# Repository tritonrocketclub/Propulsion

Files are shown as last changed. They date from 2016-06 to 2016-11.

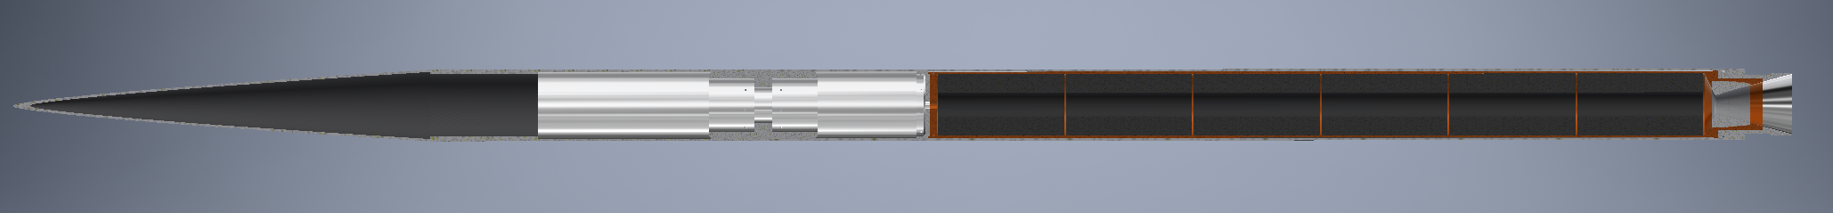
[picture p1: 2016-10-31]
Launches/8-inch-flight/Design/CAD/Vehicle/full_vehicle.PNG

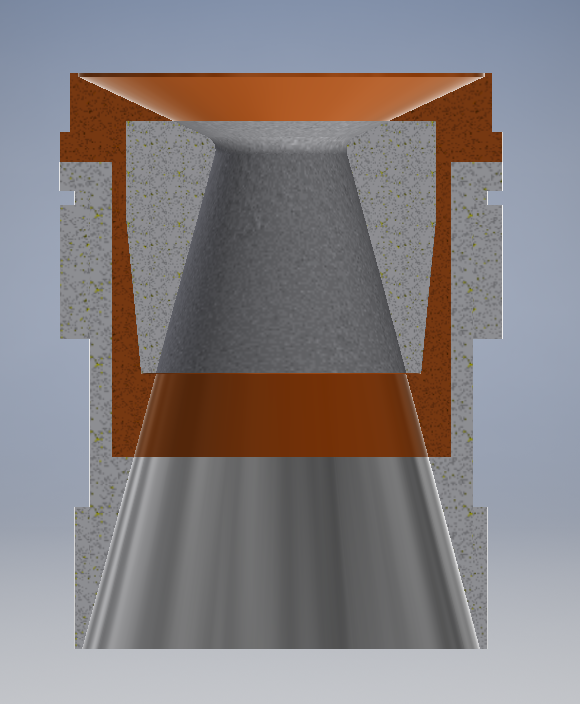
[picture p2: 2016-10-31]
Launches/8-inch-flight/Design/CAD/Vehicle/nozzle.png

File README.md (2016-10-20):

# Propulsion

Triton Rocket Club's Propulsion Team Repository.

## Overview
The Propulsion Team is resposible for designing and manufacturing the propulsion system for all TRC launches. Historically, TRC has created single stage, solid motor rockets to achieve their goals. Starting in Fall of 2016, TRC will begin research into liquid propulsion systems, however, this will remain a research only project until further notice.

## Current Projects
### Intrepid Rocket
* Q-motor
* extimated altitude of 50km
* 7.5s burn time
* Aluminum APCP

### Liquid Propellant Engine
Research phase only.
* Isopropyl Alcohol and Nitrogen Tetroxide (fuel and oxidize)
* targeting 1000lb thrust
* reneratively cooled
* pressure fed

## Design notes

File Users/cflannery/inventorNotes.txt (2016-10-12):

Autodesk Inventor Tutorial:

<User Interface>
 - creating files
 - file types
  - how files are stored
 - browser and panel bar in assembly, part, presentation, and drawing environments
 
 <Inventor My Home>
  -Getting Started
  -Team Web(configure for Triton Rocket Club)
  -Help Documentation
  
 <New>
  -parts
  -assemly
  -presentation
  -drawing
  
  -Expand new panel to select more advanced templates (Create TRC templates)
  
 <Recent Documents>
  - can be opened immediately
  - My Home Screen will remain in the bottom as a tab
 <Recent Documents/>
 
 <Environments>
  <File Extensions>
   Assembly Files .iam
   Part Files .ipt
   Drawing Files .dwg
	-industry standard file type for drawings
   Inventor Drawing Files .idw
  <File Extensions/>
  <Template Files>
   TRC has/will be making their own templates for part files and drawing files
   Ensures consistent units
  <Template Files/>
  <Part Modeling Environment>
   Create and edit 3D parts
   interface will adjust to present tools for your current task
  <Part Modeling Environment/>
  <Assembly Modeling Environment>
   Build and edit 3D assembly models 
   components are referenced in assemblies, part data still lives in part file
  <Assembly Modeling Environment/>
  <Presentation Environment>
   Create exploded assembly views
   record animations
   presentation files reference assembly files
  <Presentation Environment/>
  <Drawing Environment>
   Create 2D drawings of parts and assemblies
   References parts, assemblies, and presentation files.
  <Drawing Environment/>
 
 <Project Files>
  Dependencies between assemblies and part files will be come complicated.
  Use a projcet file to define file dependency
  
  You MUST have an active project before creating any files
   - on the bottom of the "Create New File" Dialogue
 <Project Files/>
 
 <File Types>
 
 <File Types/>

  <Parts>
   Parts are their own entity
   Stored in their own files
   Can be used in multiple Assemblies
   Changes to part files will be reflected in Assemblies
  <Parts/>
  <Assemblies>
   Can be referenced in other assembly files, presentation files, and drawing files

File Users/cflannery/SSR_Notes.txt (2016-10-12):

System Design Review Notes

Big picture, high level design for 8-inch launch

Intrepid:
* shall be a rocket
* must be scalable for the "space launch"
* altitude goal/motor class?
 - defined by motor class
 - Q motor
 - 125k feet
 
 stability margin
 
 2 stage rocket
 
Jared says we can't do large 2 stage bc of faa

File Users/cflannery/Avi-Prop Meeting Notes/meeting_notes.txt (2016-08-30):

Meeting Notes:

SLV:
- prop may have to take over SLV
- should consider making a two stage rocket
- I will look into the quantitative justification for using a two stage rocket

Second stage:
- good engineering challenge
- mechanical design
- electrical design
- actuators?
- second stage engine can extend into interstage
- interstages are sexy

- actuators are complex
 - they are a good engineering challenge
 
Flight Computer:
- triple redundancy?
- interstage controller
- meche design
 - have people design mechanical enclosuers
- RIOs
 - thermal
 - pducer
 - transmit
 - video
  
- Second stage flight computer:
 - clone of first stage

- This design can be brought to the design review with SpaceX

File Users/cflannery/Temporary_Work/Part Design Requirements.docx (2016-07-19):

I) Nozzle Retaining Ring
  A) Must have at least ½” wall thickness
  B) Forward end must have space for a ¼” or thicker o-ring on the outer diameter
    1) O-ring groove requirements
      (a) Groove height must be <80% of thickness of ring to ensure compression
      (b) Groove OD cannot allow for less than 50% of retainer to come into contact with nozzle
      (c) Groove must give adequate compression to hold o-ring on with a small amount of stretch
        (i) Reference McMaster Carr website for “actual” dimensions of o-rings
    2) Purpose is for sealing the motor’s aft end
    3) Thicker o-rings for larger motors is not a requirement, but margins become tight
  C) Must be long enough to contain pins at least 2x pin diameter from top or bottom
    1) Makes sure that there is no failure in the retainer due to yielding
    2) Drilling is not perfectly accurate, and leeway must be given for drill to work properly
II) Nozzle Basic Requirements
  A) Phenolic must be glued on top of the graphite section to ensure that there are no joints parallel to flow direction
  B) Graphite and phenolic inserts must be in compression during firing by use of steps
    1) Step thickness must be ~10% of motor diameter
  C) A 1” length of phenolic must mate with the ID of the casting tube
    1) Ensures that no heated gas flows to the aluminum
    2) Additionally allows for pressure to reach cavity between aluminum and phenolic
      (a) If a single flow path is not generated then the phenolic must take the pressure, and will crack, leading to failure
  D) Sections must be mated using a high temperature epoxy (IE JB-weld), and will have final profile machined as a single piece
  E) Nozzle internal profile does not need to be exact, but no sharp angles can be created in flow path Part Specific Nozzle Requirements
III) Specific Requirements
  A) Graphite Requirements
    1) Minimum thickness must be greater than 10% of motor diameter
    2) Minimum thickness at throat must be greater than 25% motor thickness, or 6”, whichever is smaller
      (a) Only allowance is if the throat is greater than 4”, then a 2” thickness is required
    3) Section must be long enough that 15o diverging half angle is reached 1” before bottom of nozzle
    4) Section must be long enough so that aft end is 166% ID of the throat
    5) OD must be roughed for gluing into phenolic
  B) Phenolic requirements
    1) 1.5” sections must be

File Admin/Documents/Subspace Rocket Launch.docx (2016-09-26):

# Subspace Rocket Launch

Triton Rocket Club

31 August 2016

# Preface

## Vehicle Designation

Henceforth, this launch vehicle will be referred to as No More Mr Nice Guy. Taking a page from SpaceX, this vehicle is named after a ship from Iain M. Banks’ Culture Series.

# Section 1: Project Overview

## 1.1 Introduction

The Triton Rocket Club is pursing the goal of being the first undergraduate university organization to launch a rocket past the Van Karmen line, 100 km, which is commonly known as the edge of space. In working towards achieving this goal, the club has been building incrementally larger solid motor rockets, making improvements each time based on empirical data.

This document outlines the design of the final launch before the club attempts the space shot.

## 1.2 Design Teams

This section will outline the design teams for the project

## 1.3 Design Reviews

This section will outline the standard design review process for any system on the rocket

## 1.4 Launch Readiness Review

This section will outline the process for determining launch readiness of No More Mr Nice Guy.

## 1.5 Mission Success/Failure

How to determine if the mission is a success or failure. A successful mission will permit TRC to continue with the development of the Space Shot Vehicle.

# Section 2: Design Criteria

## 2.1 Altitude

The target altitude for No More Mr Nice Guy is 50 km.

## 2.2 Two Stage Design

The TRC Two-Stage Vehicle is designed with the goal of achieving a higher altitude with a smaller mass ratio. Furthermore, building a two-stage rocket provides a unique challenge for all the engineering groups. This allows for the organization to perform one of its main functions; the development of good engineers. The discussion below covers the design criteria for each department and team with in TRC in relation to building a two stage vehicle.

## 2.3 Propulsion

Propulsion for No More Mr Nice Guy should demonstrate remote ignition capabilities of the second stage.

## 2.3.1 First Stage

Initial ascent.

## 2.3.2 Second Stage

Secondary ascent. Apogee of at least 50 km.

## 2.3.3 Thermal

Propulsion thermal team is responsible for instrumenting the vehicle and measuring thermal data against models

## 2.4 Avionics

Avionics has a lot of stuff.

- Design

## 2.4.1 Flight Computer

## 2.4.2 RIO

## 2.4.3 Instrumentation

## 2.4.4 Telemetry

## 2.4.5 Power

## 2.4.6 RF

Avionics RF is responsible for communication between the rocket and the ground station.

## 2.5 Space Launch Vehicle

The Space Launch Vehicle is the design of both the first and second stage of No More Mr Nice Guy. The design should ensure that cost, in terms of materials, weight, and size, are minimized by using a two-stage vehicle as opposed to a single stage.

Possible to reduce mass by using COPV?

## 2.6 Structures

Rephrase to conform to highlight design criteria

Structures for No More Mr Nice Guy requires a launch tower that can accommodate a two-stage vehicle. The current launch tower is capable of housing a two-stage rocket. Holes must be drilled to adjust the launch rails to the appropriate rocket diameter. The logistics of transportation of the tower currently requires two trucks due to each half of the tower being 8’ tall and having a base of 3’ x 3’. Lifting the tower with a heavy rocket inside it will require a few people and ropes, potentially with the assistance of a winch.

## 2.7 Launch Operations

Launch Operations primary function is to ensure launch conditions are sufficient for launch. Launch Operations will also receive telemetry from the rocket and monitor its performance.

## 2.8 Payload

TBD if a scientific payload will be launched on No More Mr Nice Guy.

# Section 3: Data Analysis and Processing

What data are we getting back from this launch, why, and what are we going to do with it.

- Confirmation of design for Space Shot
- Identification of any failure modes
- Engineering challenge for students

# Section 4: Launch Facility

Details about the launch facility. Black rock? Must support altitude of 50 km.

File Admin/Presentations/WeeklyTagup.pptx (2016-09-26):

## Propulsion Weekly Tagup

12 September 2016

## Agenda

- Two-Stage Calculations
- NASA Sounding Rockets

## Two-Stage Calculations

- Assume two equal stages (nonideal)

## NASA Sounding Rockets

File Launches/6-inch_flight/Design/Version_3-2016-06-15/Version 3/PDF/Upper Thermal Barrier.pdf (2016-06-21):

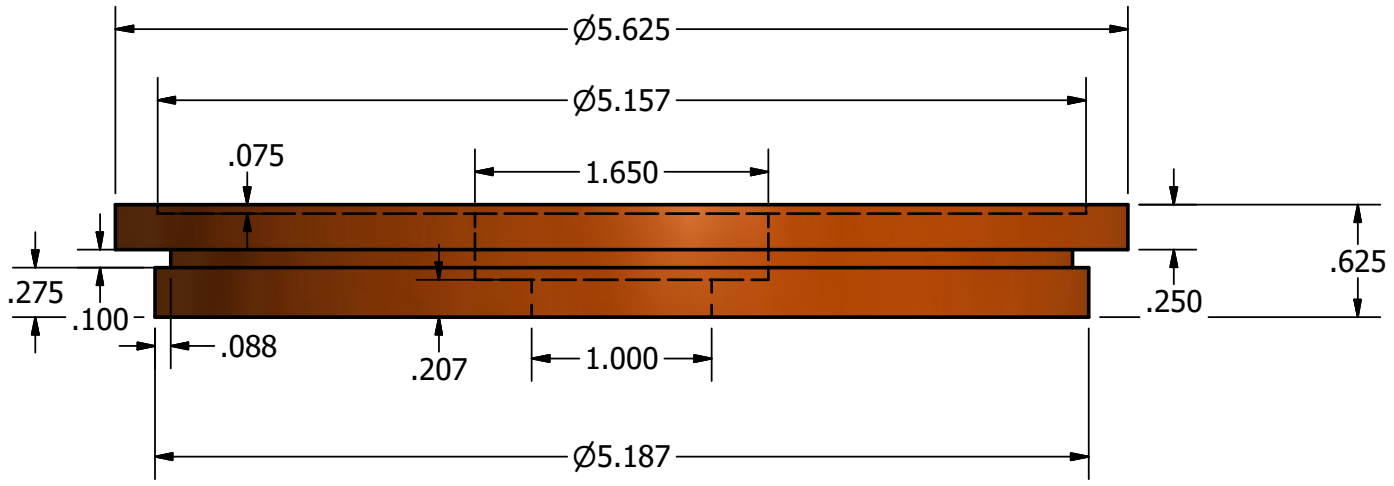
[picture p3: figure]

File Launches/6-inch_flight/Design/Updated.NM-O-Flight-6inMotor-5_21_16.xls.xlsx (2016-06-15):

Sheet: Bates Grain Kn Calculator
Bates Grain Kn Calculator | Version 2K |  |  |  |  | 541.1623662 | Max Psi
 |  |  |  |  |  | 527.5492347 | Avg Psi
 |  |  |  |  |  | 1435.83065 | Max Thrust (lbf) |  |  |  |  |  |  |  |  | Throat
Number of Grains: | 4 |  | boundry layer |  |  | 1396.14471 | Avg Thrust (lbf) |  |  |  |  |  |  |  |  | Diameter
Grain OD (OD Casting: | 5.187 |  | 0.005 |  |  | 4.50 | Burn Time (s) |  |  |  |  |  |  |  |  | Rate
Core Diameter: | 3.250 | Core Di (in) |  |  |  | 6283.861349 | Total Impulse (lbf*s) |  |  |  |  |  |  |  |  | 0
Grain Length: | 10 | 3 |  |  |  | 0 | Isp |  |  |  |  |  |  |  |  |  |  |  |  |  |  | outer
Nozzle Throat Diameter: | 1.5 | 3.2 |  |  |  |  |  |  |  |  | BurnA1 | BurnA2 | Each grain |  |  | equ nozzle | Nozzle |  | nozzle |  |  | nozzle
Final Nozzle Throat Diameter | 1.5 | 3.3 |  | Burn | OD-Initial | Length | Core dia | Outside | End area | Core End | End area | Core burn | Total burn | Area x number | Web | Throat | Throat | Kn Ratio (w/ boundary | throat |  |  | throat
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

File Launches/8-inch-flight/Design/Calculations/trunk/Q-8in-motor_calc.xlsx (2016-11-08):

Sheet: Bates Grain Kn Calculator
Bates Grain Kn Calculator |  | Version 2K |  |  |  |  | Outputs |  |  |  |  |  |  |  |  | Okay to Calculate: |  | TRUE
Mission: |  | Q-Motor
 |  |  |  |  |  |  | Burn Increment: |  | 0.1431 | [in/step] |  | Max Psi: |  | 642.2202061
Number of Grains: |  | 6 | # | Grain Core Diameters (in) |  |  | Initial burn surface: |  | 1103.1467 |  |  | AVG Psi: |  | 586.5227509 |  | Error Checking
Grain OD (ID Casting): |  | 6.9 | [in] |  |  |  | Nozzle throat area: |  | 4.011 | *no boundry |  | Max Thrust (lbf): |  | 3972.217478
Core Diameter: |  | 2.75 | [in] | 3 |  | # | Initial Kn: |  | 277.4459259 |  |  | Avg Thrust (lbf): |  | 3600.392678
Grain Length: |  | 14 | [in] | 3 |  | # | Kn Max: |  | 334.5264738 |  |  | Burn Time (s): |  | 9.236801475
Nozzle Throat Diameter: |  | 2.26 | [in] | 3 |  | # | Final Kn: |  | 322.2044444 |  |  | Total Impulse (lbf*s): |  | 32626.64886
Final Nozzle Throat Diameter: |  | 2.26 | [in] | 3.4 |  | # |  |  |  |  |  | Erosive need below 1.4: |  | 1.184060106
Nozzle Exit Dia: |  | 6 | [in] | 3.8 |  | # | "Ideal" Bates length: |  | 11.7250 | (See Note 4)
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

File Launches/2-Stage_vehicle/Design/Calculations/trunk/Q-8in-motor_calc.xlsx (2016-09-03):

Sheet: Bates Grain Kn Calculator
Bates Grain Kn Calculator |  | Version 2K |  |  |  |  | Outputs |  |  |  |  |  |  |  |  | Okay to Calculate: |  | TRUE
Mission: |  | Q-Motor
 |  |  |  |  |  |  | Burn Increment: |  | 0.1257 | [in/step] |  | Max Psi: |  | 745.9793426
Number of Grains: |  | 6 | # | Grain Core Diameters (in) |  |  | Initial burn surface: |  | 1261.6470 |  |  | AVG Psi: |  | 698.3950626 |  | Error Checking
Grain OD (ID Casting): |  | 7.062 | [in] |  |  |  | Nozzle throat area: |  | 4.011 | *no boundry |  | Max Thrust (lbf): |  | 4622.400088
Core Diameter: |  | 3.416666667 | [in] | 3 |  | # | Initial Kn: |  | 317.3093915 |  |  | Avg Thrust (lbf): |  | 4301.691088
Grain Length: |  | 14 | [in] | 3 |  | # | Kn Max: |  | 357.8910079 |  |  | Burn Time (s): |  | 7.500291867
Nozzle Throat Diameter: |  | 2.26 | [in] | 3 |  | # | Final Kn: |  | 346.6650359 |  |  | Total Impulse (lbf*s): |  | 32181.17732
Final Nozzle Throat Diameter: |  | 2.26 | [in] | 3.4 |  | # |  |  |  |  |  | Erosive need below 1.4: |  | 1.30036548
Nozzle Exit Dia: |  | 9 | [in] | 3.8 |  | # | "Ideal" Bates length: |  | 12.3013 | (See Note 4) |  | Isp[s]: |  | 217.8164393 | [s]
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

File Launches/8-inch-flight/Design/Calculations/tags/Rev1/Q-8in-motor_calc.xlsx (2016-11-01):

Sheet: Bates Grain Kn Calculator
Bates Grain Kn Calculator |  | Version 2K |  |  |  |  | Outputs |  |  |  |  |  |  |  |  | Okay to Calculate: |  | TRUE
Mission: |  | Q-Motor
 |  |  |  |  |  |  | Burn Increment: |  | 0.1431 | [in/step] |  | Max Psi: |  | 642.2202061
Number of Grains: |  | 6 | # | Grain Core Diameters (in) |  |  | Initial burn surface: |  | 1103.1467 |  |  | AVG Psi: |  | 586.5227509 |  | Error Checking
Grain OD (ID Casting): |  | 6.9 | [in] |  |  |  | Nozzle throat area: |  | 4.011 | *no boundry |  | Max Thrust (lbf): |  | 3923.160089
Core Diameter: |  | 2.75 | [in] | 3 |  | # | Initial Kn: |  | 277.4459259 |  |  | Avg Thrust (lbf): |  | 3550.87038
Grain Length: |  | 14 | [in] | 3 |  | # | Kn Max: |  | 334.5264738 |  |  | Burn Time (s): |  | 9.236801475
Nozzle Throat Diameter: |  | 2.26 | [in] | 3 |  | # | Final Kn: |  | 322.2044444 |  |  | Total Impulse (lbf*s): |  | 32626.64886
Final Nozzle Throat Diameter: |  | 2.26 | [in] | 3.4 |  | # |  |  |  |  |  | Erosive need below 1.4: |  | 1.184060106
Nozzle Exit Dia: |  | 9 | [in] | 3.8 |  | # | "Ideal" Bates length: |  | 11.7250 | (See Note 4)
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

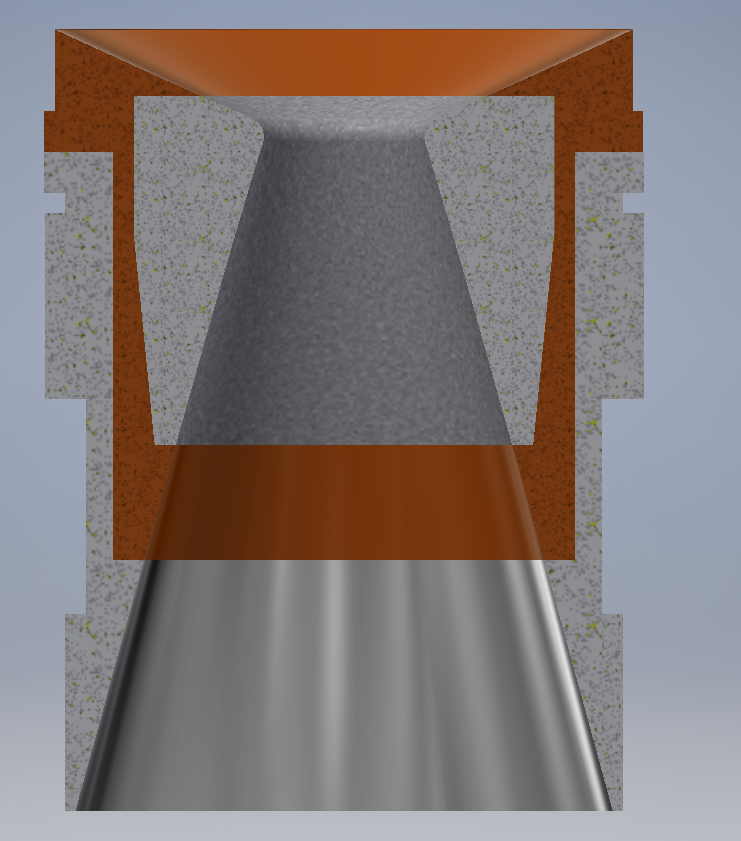
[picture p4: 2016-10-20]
Launches/8-inch-flight/Design/CAD/Vehicle/Nozzle/sectionView.PNG

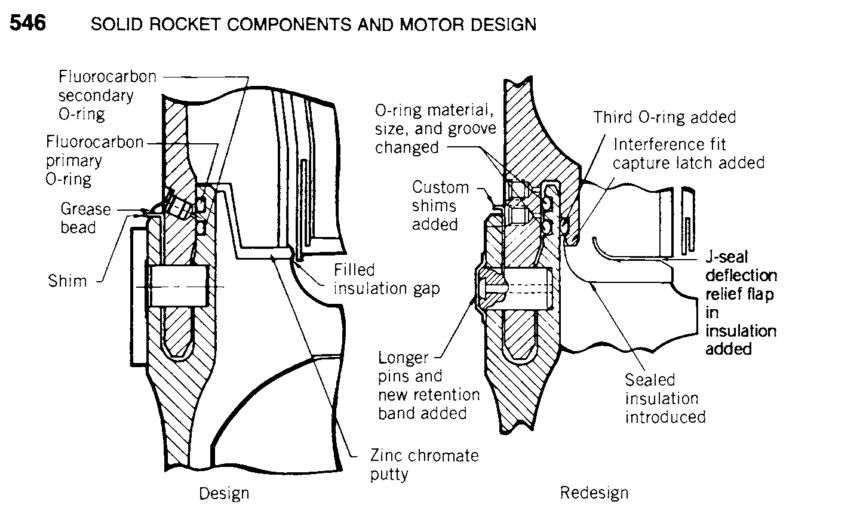
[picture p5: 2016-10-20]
Launches/8-inch-flight/Design/CAD/Vehicle/Nozzle/O-ring_SRBs.PNG

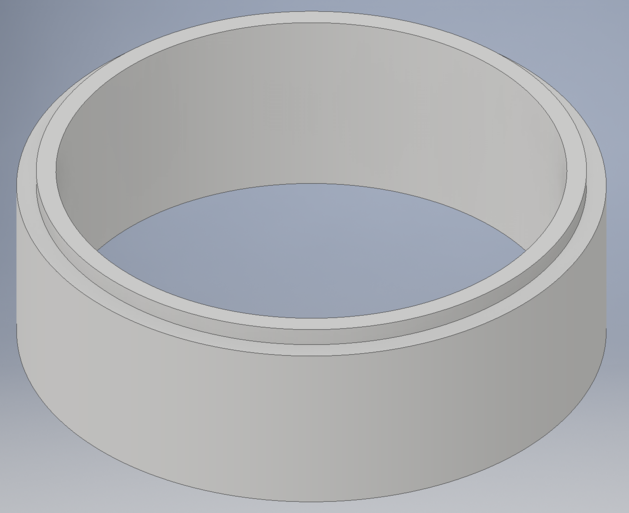
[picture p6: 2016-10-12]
Users/blieu/Images/Retainer.PNG

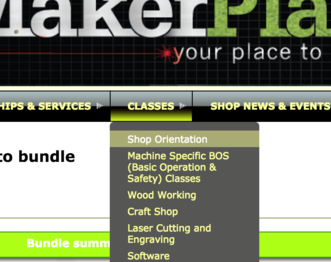
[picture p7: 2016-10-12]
Users/blieu/Images/classes.png

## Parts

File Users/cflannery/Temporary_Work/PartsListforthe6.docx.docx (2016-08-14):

# 6” Comprehensive Parts List

Reference for 8” and 10”

https://drive.google.com/folderview?id=0BxXyjHIezGQrbno0R293bmlCUVU&usp=drive_web

# Propulsions

- Graphite throat for nozzle - FE250 lathed from 4x4x6” block for 6” static fire from Kevin Anderson <KevinA@etm-lb.com>, bought G330 (higher grade, more density needed) for 6” flight, G330 will be needed for all further flights as well
- Phenolic carrier for nozzle - “Machinable Garolite (LE)” from McMaster-Carr, lathed from multiple blocks 1.5” thick epoxied onto each other, could possibly buy rod version instead for future as it will be one piece : http://www.mcmaster.com/#garolite/=121yfgj
- Aluminum carrier for nozzle - from 6061-T6 stock at IMS, lathed to design
- Forward Bulkhead, Aluminum 6061-T6 stock at IMS lathed to design
- Casting Tubes ( Paper Reinforced XX Tubing 5.375 OD x 5.187 ID x .093 Wall 9 Feet Min Order ) ordered from http://k-mac-plastics.com/xx-laminate-tubes.htm
- Phenolic Liners (5.375 ID x .125 Wall) ordered from: Scott Kormier of Loki Rocketry
- Aluminum 6061-T6 motor casing- 6” OD, 3/16”(.1875) wall thickness: drilled holes in side for pin slots
- Pull Out Dowel Pins from Mcmaster-Carr for nozzle and forward bulkhead
  - http://www.mcmaster.com/#standard-dowel-pins/=121yho0

GENERAL: Aeropoxy+Filler

White Lithium Grease

multipurpose (silicone) orange http://www.mcmaster.com/#o-rings/=121yjuk (when in doubt lower 0 rings size)

Igniters (from Jon Newman)

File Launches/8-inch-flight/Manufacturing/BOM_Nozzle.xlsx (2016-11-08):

Nozzle Part | Material | Dimensions | Supplier | Notes
Graphit Throat for Nozzle | G330 | 5.26"x5.26"x4.25" | Kevin Anderson contacted at KevinA@etm-lb.com | http://www.tokaicarbon.co.jp/en/products/fine_carbon/isotropic.html
Phenolic Carrier | Machinable Garolite | 7.5"x7.5"x6" | http://www.mcmaster.com/#garolite/=13byhm6 | Either buy a rod or multiple 1.5'' thick blocks epoxied onto each other
Aluminum Carrier | Aluminum 6061-T6 | 7.5"x7.5"x6.9" | http://www.mcmaster.com/#aluminum-alloy-6061/=13bz6eb | Or Stock at IMS
Forward Bulkhead | Aluminum 6061-T6 |  | Same as above
Motor Casing | Aluminum 6061-T6 | 8” OD, 3/16”(.1875) Thickness | Same as above | Drilled holes in side for pin slots
Aluminum Skirt | Aluminum 6061-T6 | 7.5"x7.5"x2.5" | Same as above
Aluminum Retainer | Aluminum 6061-T6 | 7.5"x7.5"x2.734" | Same as above
Motor Liner | Phenolic Liner |  | http://www.rocketmotorparts.com/Phenolic_Liners_Uncut_Lengths/cat1577810_1455513.aspx
Casting Tubes | Pheolic Laminate Tubes Paper Reinforced XX | 5.375 OD, 5.187 ID, 0.093 Thickness | http://k-mac-plastics.com/xx-laminate-tubes.htm | Stock # : KM-22621BQ
Pull Out Dowel Pins | Stainless Steel (Type 316, 18-8, or Type 416) |  | http://www.mcmaster.com/#standard-dowel-pins/=121yho0 | For Nozzle and Forward Bulkhead
Phenolic Cap | Machinable Garolite | 7.5"x7.5"x2.5"
General
Aeropoxy + Filler
White Lithium Grease
O-Ring | Multipurpose Silicone |  | http://www.mcmaster.com/#o-rings/=121yjuk | If in doubt lower ring size
Igniters

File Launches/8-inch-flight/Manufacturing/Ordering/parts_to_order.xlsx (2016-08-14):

Bill of Materials
Item | Description | Purpose | Manufacturer | Manufacturer P/N | Supplier | Qty | Unit Cost | Total Cost | Link
1 | Graphite Block | Nozzle Throat | Electro-Tech Machining | G330 | Kevin Anderson | 1 |  |  | Kevin Anderson <KevinA@etm-lb.com
2 | Machinable Garolite (LE) | Phenolic Carrier for Nozzle | - | - | McMaster-Carr | 1
3 |  |  |  |  | Industrial Metal Supply (IMS) | 1
4
5
6
7
8
9
10
11
12
13
14
15
16
17
18
19
20
21
22
23

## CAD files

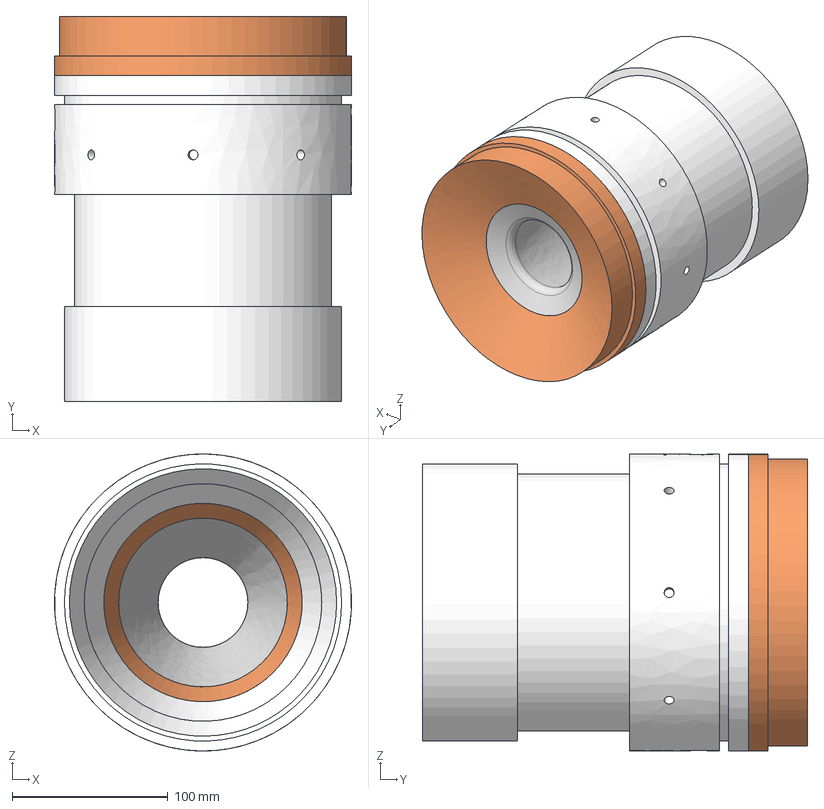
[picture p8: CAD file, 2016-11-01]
Launches/8-inch-flight/Design/CAD/Vehicle/Nozzle/trunk/nozzle.igs
190.5 x 247.2 x 190.5 mm

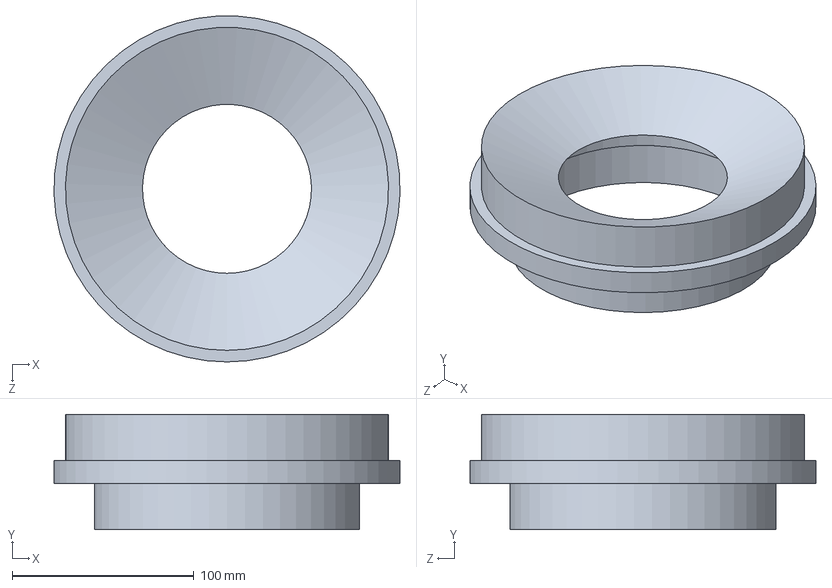
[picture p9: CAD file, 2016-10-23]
Users/cflannery/Temporary_Work/Intrepid_temp/Nozzle/SolidWorks/phenolic_liner.SLDPRT
190.4 x 63.5 x 190.3 mm

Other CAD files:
Launches/8-inch-flight/Design/CAD/Nozzle/trunk/Drawings/Aluminum Skirt.dwg
Launches/8-inch-flight/Design/CAD/Vehicle/Nozzle/trunk/Drawings/ALUMINUM_RETAINER.dwg
Users/cflannery/Temporary_Work/Intrepid_temp/Nozzle/SolidWorks/aluminum_carrier.SLDPRT
Launches/8-inch-flight/Design/CAD/Vehicle/Nozzle/trunk/Drawings/ALUMINUM_CASING.dwg
Users/cflannery/Temporary_Work/Intrepid_temp/Nozzle/SolidWorks/aluminum_retainer.SLDPRT
Launches/8-inch-flight/Design/CAD/Vehicle/Nozzle/trunk/Drawings/PHENOLIC_CARRIER.dwg
Users/cflannery/Temporary_Work/Intrepid_temp/Nozzle/SolidWorks/aluminum_boattail.SLDPRT
Launches/8-inch-flight/Design/CAD/Vehicle/Nozzle/trunk/Drawings/GRAPHITE.dwg
Users/cflannery/Temporary_Work/Intrepid_temp/Nozzle/SolidWorks/graphite.SLDPRT
Launches/8-inch-flight/Design/CAD/Vehicle/Nozzle/trunk/Drawings/PHENOLIC_CAP.dwg
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

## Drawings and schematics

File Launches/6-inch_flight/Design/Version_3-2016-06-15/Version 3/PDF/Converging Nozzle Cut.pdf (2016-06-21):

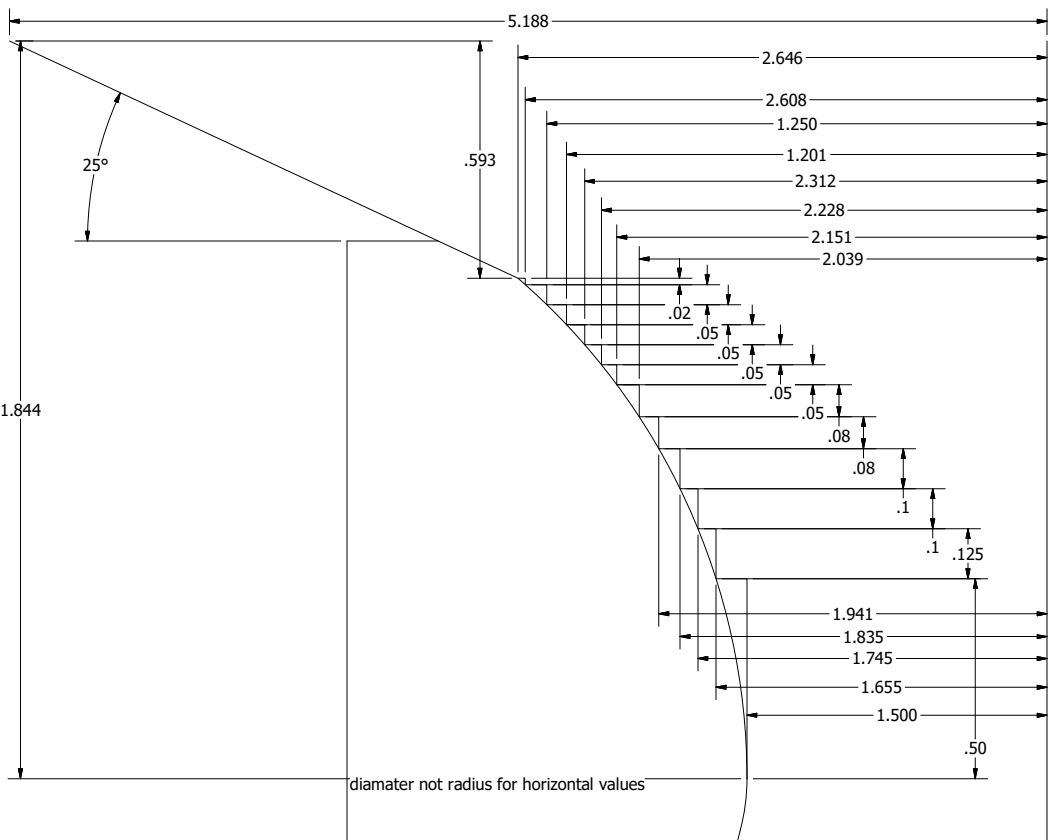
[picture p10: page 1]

diamater not radius for horizontal values

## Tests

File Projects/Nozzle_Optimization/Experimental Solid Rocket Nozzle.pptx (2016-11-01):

## Experimental Solid Rocket Nozzle

By: Cameron Flannery, Harrison Box

## Agenda

- Vehicle Overview
- Nozzle Design Overview
  - Dimensions
  - Thermal
  - Fluid Flow
- Risks

## Vehicle Overview (Major Components)

17’

7’8”


Nosecone

Recovery System

Avi-bay

BATES grains

General
- 2 piece aluminum airframe
- Aluminum section adapter
- ¾ power series nosecone
- Carbon fiber
- Note: Fins still under design review

Section Adapter

Propulsion
- Q-Class Motor
- APCP (Aluminum Fuel/Ammonium Perchlorate Oxidizer)
- Ablatively cooled nozzle
- BATES grains

Ablative Nozzle

## Nozzle Overview

Phenolic
(2-pieces)


Graphite Throat

Aluminum Retainer

Aluminum Carrier

Aluminum Skirt

## Dimensioning

Calculating Optimal Expansion Ratio*:

2.30”

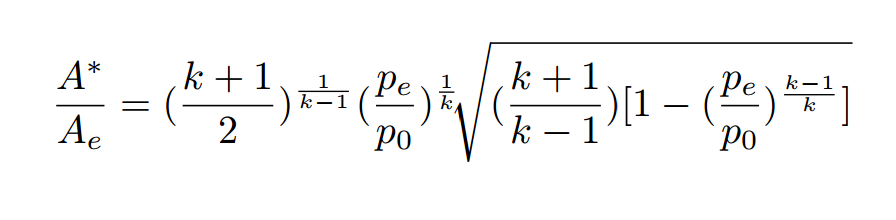
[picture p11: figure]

Ideal**: 3.1 – calculated with combustion products properties
Actual: 2.934

- Under-expansion results from manufacturing capabilities.
- Exact impact on performance is difficult to calculate due to liquid combustion products (Al)
- Performance decrease of ~5% expected

6.75”

*equation from Rocket Propulsion Elements
** at sea-level

## Nozzle Design – Stresses

Hoop Stress:

Material Properties:
- Phenolic Liner: Liner thickness; ¼”
- Heat Transfer Through Phenolic Liner: 0.15W/(m∗K)

## Nozzle Design – Fluid Flow

Aim:
- Prevent cavitation
- Prevent separation of flow
Analysis:
- CFD with ANSYS
  - Assumes gaseous combustion products
  - Results in approximately 10% error due to aluminum in propellant

## Design for Manufacturability

- 6061 Series Aluminum
- Phenolic and graphite relatively simple to machine
- Cone Nozzle:
  - Easy to machine with a lathe
  - No crazy contours
- Drawings created with GD&T for each part

## Risks

- Under-expansion is not quantified
  - Possible solution is to perform a static fires at sea-level with different expansion ratios
- Phenolic Thermal Barrier

## Q & A

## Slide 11

BACKUP SLIDES

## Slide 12

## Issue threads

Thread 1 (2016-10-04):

Nozzle Throat-Exit ratio optimization

cmflannery, 2016-10-04:
Nozzle throat-exit dimensions need to be reviewed.

cmflannery, 2016-10-04:
starting work on nozzle optimization

Bslieu99019, 2016-10-11:
**Important Links**

1. [8-inch Motor Calcs](https://github.com/tritonrocketclub/Propulsion/tree/master/Launches/8-inch-flight/Design/Calculations/trunk)
2. [Nozzle wiki](https://github.com/tritonrocketclub/Propulsion/wiki/%5BDocumentation%5D-8-inch-Rocket)

Bslieu99019, 2016-10-28:
Aluminum 6061T-6 Carrier Calculations:

Hoop stress w/ FS = 2.0 => 12.8 ksi

Thermal Stress w/ 300 F & FS = 2 => 31.7 ksi (various with temperature)
Aluminum Melting point = 1080 - 1205 °F

Tensile Strength Aluminum = 40 kpsi
Minimum thickness w/ FS = 2: 0.133125 inches

Ultimate Bursting Pressure = 3000 psi
Yield Bursting Pressure = 2666.67 psi
Maximum Pressure Experienced = 710 psi

jacquelynfirst, 2016-11-01:
I worked on the aluminum carrier with Ryan and this is what we found so far. We got a thermal stress of about 55,000psi with a temp estimate of 430 degree F change. Also Hoop stress was 7,114psi with factor of safety of 5.6.

Happy Halloween!

dtt005, 2016-11-03:
Best diameter for diverging section = 5.618in
Optimum Expansion Ratio = 6.177
Pressure experienced of aluminum skirt at exit plane = 16.546PSI (12.589% higher than atmospheric pressure)

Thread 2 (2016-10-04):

Getting more done in GitHub with ZenHub

cmflannery, 2016-10-04:
Hola! @cmflannery has created a [ZenHub](http://www.zenhub.com) account for the **tritonrocketclub** organization. ZenHub is the only project management tool integrated natively in GitHub – created specifically for fast-moving, software-driven teams.

----

#### How do I use ZenHub?

To get set up with ZenHub, all you have to do is **[download the browser extension](https://www.zenhub.com?utm_source=ZHOnboarding)** and log in with your GitHub account. Once you do, you’ll get access to ZenHub’s complete feature-set immediately.

#### What can ZenHub do?

ZenHub adds a series of enhancements directly inside the GitHub UI:

- Real-time, customizable task boards for GitHub issues;
- Multi-Repository burndown charts, estimates, and velocity tracking based on GitHub Milestones;
- Personal to-do lists and task prioritization;
- Time-saving shortcuts – like a quick repo switcher, a “Move issue” button, and much more.

### [Add ZenHub to GitHub](https://www.zenhub.com?utm_source=ZHOnboarding)

_Still curious? See [more ZenHub features](https://www.zenhub.com/features?utm_source=ZHOnboarding) or read [user reviews](https://chrome.google.com/webstore/detail/zenhub-for-github/ogcgkffhplmphkaahpmffcafajaocjbd/reviews). This issue was written by your friendly ZenHub bot, posted by request from @cmflannery._

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

Closed 2016-10-11.

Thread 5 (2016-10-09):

Avionics Integration

cmflannery, 2016-10-09:
In order to monitor motor health, the propulsion team needs chamber pressure throughout the flight. Temperature readings could also be used to confirm thermal calculations. This epic tracks the integration of the pducer into the vehicle and avionics.

The propulsion team is responsible for the mechanical design of the Avi-bay this year. The Avi-bay will be used to mount and chassis ground the flight computer.

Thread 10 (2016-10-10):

Mechanical Design for Avi Bay

cmflannery, 2016-10-10:
Design mechanical bay for avionics. Should fit snuggly and have mounting holes. Chassis ground.

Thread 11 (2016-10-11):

Quantify error due to erosive burning

cmflannery, 2016-10-11:
Determine if error due to throat ablation can be ignored in CFD analysis. Baseline Q-class motor using APCP fuel.

cmflannery, 2016-10-18:
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
- [Ablative Cooling Study](https://github.com/tritonrocketclub/Propulsion/tree/0f0267c2cab3b7e235d0b69af07ad0d52786ffc0/References/AblativeSolidRocketNozzles.pdf)

Regression due to ablative cooling can be estimated with this plot and the chamber pressure. Ablation is only estimated at the throat (graphite).

Chamber pressure ~= 4.815 MPa
Burn time ~= 7.5 s
 - from [motor calc sheet](https://github.com/tritonrocketclub/Propulsion/blob/0f0267c2cab3b7e235d0b69af07ad0d52786ffc0/Launches/8-inch-flight/Design/Calculations/tags/Rev1/Q-8in-motor_calc.xl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)

Estimated graphite regression ~= 0.17 mm/s
- based on chamber pressure & plot above

Total estimated regression ~= 0.17 mm/s * 7.5s = 1.275 mm

cmflannery, 2016-10-18:
Closing as "won't fix"  - Ablative cooling for such a short burn time does not result in significant loss of thrust due to throat area increase.

Closed 2016-10-18.

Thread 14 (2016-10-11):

Full Vehicle Mockup

cmflannery, 2016-10-11:
3D print scale model of the entire vehicle for fit checking.

cmflannery, 2016-10-21:
Rev01 nearing completion.
Todo:
* finalize airframe length
* finalize nozzle design
 * boat tail?
* finalize nose cone dimensions
* add fin can
* add faux mass for recovery system
* dimension and add avi components
* work out avi interface
 * how are we going to connect avi components 3-4' into the tube?

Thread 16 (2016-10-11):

Igniter

cmflannery, 2016-10-11:
The igniter for Intrepid presents a unique challenge. To launch a Q-class motor, we need to be ~1 mile away from the launch site. It is impractical to ignite the rocket using conventional methods; namely, we cannot run a cable from the launch site to mission control. The solution is going to be a wirelessly triggered system.

This challenge will be solved with support from Launch Ops and Avionics.

cmflannery, 2016-11-11:
Ignition will be triggered with a hot wire and a small solid rocket motor.

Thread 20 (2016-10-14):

Liner fitting into airframe

cmflannery, 2016-10-14:
The tolerances on the liner and the aluminum casing need to be large enough to allow the liner to slide into the airframe. Hoop stress calculation and material calculations should be completed on the liner to ensure the pressure in the combustion chamber doesn't cause the liner to fracture.

Look into other possible solutions.
* o-rings

Bslieu99019, 2016-10-15:
10/14 - Hoop Stress Calculations:
-FS of 1.5: ~ 31k psi
-FS of 2.0: ~ 42k psi
-Material Interest: Garolic G10: 32-40k psi (max allowable)

cmflannery, 2016-10-29:
**Phenolic Liner**
Liner thickness; 1/8"
Liner Length: 7' 10" = 94"

**Casting Tubes:**
Thickness: 1/8"
Length: 15"

**Grains**
Length: 14"
OD: 6.90"
ID: 2.75"

rlibman, 2016-11-01:
**Phenolic Liner Hoop Stress Calculations**

Using http://www.engineeringtoolbox.com/stress-thin-walled-tube-d_948.html

Hoop Stress = (745.9793426 psi * 7.062 in) / 2 * .25 in = 10536.2122348824 psi

Per http://www.g10fr4.com/g10_fr4_technical_data_specifications.html

19,000 psi max

Therefore a F.S. of ~1.8.

cmflannery, 2016-11-01:
The purpose fo the phenolic liner is to act as a thermal barrier between the combustion chamber and the aluminum casing. The phenolic liner doesn't need to take hoop stress. The heat transfer through the phenolic liner to the aluminum should be calculated and then the hoop stresses in the aluminum liner should be compared against its yield stress.

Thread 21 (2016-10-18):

Avionics Integration Design Parameters

mphalen, 2016-10-18:
The Chamber temperature and pressure ranges are needed to start planning out the avionics package. A budget estimate and desired form-factor are also welcome, but not immediately required, at this stage.

mphalen, 2016-10-26:
Chamber and pressure maximums are specified as ~710psi and ~2000C,

Closed 2016-10-26.

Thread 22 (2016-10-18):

Nozzle Dimensions and Fitting in CAD

cmflannery, 2016-10-18:
Update master sketch in Inventor and recreate assemblies and parts.

cmflannery, 2016-10-18:
[Link to rev02 directory](https://github.com/tritonrocketclub/Propulsion/tree/d85780c77f0e4c64ab95ed61d2e18549b5a94648/Launches/8-inch-flight/Design/CAD/Nozzle/tags/rev01)

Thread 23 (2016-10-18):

3D printed mock-up of nozzle

cmflannery, 2016-10-18:
Use 3D printers at library to print a mock-up of the nozzle. Scaled down to fit on printbed. Use support material where necessary.

cmflannery, 2016-10-18:
Reserve 3d printers at library [here](http://ucsd.evanced.info/dibs/Login)

Bslieu99019, 2016-10-19:
Printers Avaliable: Maker Bot: Ultimaker 2 (x1) and Replicator 2 (x2)

Instructions:
1) Two people will schedule a 3 hour block, back to back, to allow for 6 hours of printing (see above).
2) Convert Inventor file to .STL and ask model to be scaled down

Bslieu99019, 2016-10-25:
Room reserved tomorrow 10/25 3-6pm for anyone who needs to 3D print their part.

Closed 2016-10-30.

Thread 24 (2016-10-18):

GD&T Drawings of Optimized Nozzle

Bslieu99019, 2016-10-18:
It is important to create a method of communication between designer and manufacturer to minimize manufacturing errors. Read up on GD&T under references>standards for more information.

Bslieu99019, 2016-10-22:
**Components**
1. Aluminum Skirt -Danny
2. Graphite - Vickie
3. Phenolic (Both) - Hao & Jesse
4. Aluminum Carrier
5. Aluminum Retainer

**Other**
1. Aluminum Airframe

ryanjerickson, 2016-10-25:
Finished Rev.1 of Aluminum carrier

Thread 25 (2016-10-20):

Forward bulkhead seal

cmflannery, 2016-10-20:
It is important that combustion gasses don't pass the forward bulkhead. We should make sure our design prevents this. We should determine if our design is sufficient.

[SRB O-ring](https://github.com/tritonrocketclub/Propulsion/tree/master/Launches/8-inch-flight/Design/CAD/Nozzle/O-ring_SRBs.PNG)
-from RPE

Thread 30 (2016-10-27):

Section Adapter

cmflannery, 2016-10-27:
Design adapter to connect motor and recovery airframe sections

Bslieu99019, 2016-10-28:
Current Design: Inadequate For Requirements

Optimizing Requires Consideration in:
-Length
-Buckling
-Loads
-Slip
-Moment of Inertia
-Thickness

More info coming soon.

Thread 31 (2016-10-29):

Pressure Sensing

cmflannery, 2016-10-29:
Pressure measurements of the motor chamber.

cmflannery, 2016-10-29:
Need tube diameter/thread types.

mphalen, 2016-11-01:
Zirconia ceramic tube diameter set to be 1" and wall thickness is 1/4"
Thread types have yet to be decided but they can be made to order.

Length of 8" is tentative, subject to change with thermodynamic analysis.

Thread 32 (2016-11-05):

Pressure Transducer Thermodynamics

mphalen, 2016-11-05:
Need thermal transfer coefficient for motor exhaust.
Thermodynamic Analysis of Prop-Avionics Integration.

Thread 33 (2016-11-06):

RASAero Crashing when running simulations

cmflannery, 2016-11-06:
RASAero crashes when running flight simulations with our motor files.

cmflannery, 2016-11-07:
Resolved: replaced tabs between time value and thrust with single space

Closed 2016-11-07.

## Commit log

2016-06-15 General update
    added folder structure and old motor calculations
    [Updated.NM-O-Flight-6inMotor-5_21_16.xls.xlsx, Updated.NM-Q-8in-Motor-Prop-Calcs (1).xlsx, Updated.NM-S-10in-Motor-Prop-Calcs (1).xlsx]
2016-06-16 Add files via upload
    Based on designs by Jared Shapiro
    [nozzle 8in version 1.ipt]
2016-06-21 Admin info added
    see files
    [Member_Info.xlsx]
2016-06-28 Updated projectMaster
    [projectMaster.xlsx]
2016-06-28 Summer Availability
    [Member_Info.xlsx]
2016-06-28 Updated Member Info
    [Member_Info.xlsx]
2016-06-28 Retry of Updating Member Info
    [Member_Info.xlsx]
2016-07-04 new references
    [BatesCalc2K_template.xls, Updated.NM-Q-8in-Motor-Prop-Calcs (1).xlsx]
2016-07-05 Updated summer availability
    [Member_Info.xlsx]
2016-07-05 motor calculations
    working - motor calculations
    [Q-8in-motor_calc.xlsx]
2016-07-05 Motor calc updates
    [Q-8in-motor_calc.xlsx]
2016-07-06 calc updates
    [Q-8in-motor_calc.xlsx]
2016-07-06 updated projects
    [projectMaster.xlsx]
2016-07-06 project master
    [projectMaster.xlsx]
2016-07-07 Updated Motor Calc Sheet
    [Q-8in-motor_calc.xlsx]
2016-07-08 8 inch Nozzle CAD Files
    [Aluminum Carrier 8-inch v1.ipt, Aluminum Retainer 8-inch v1.ipt, Aluminum Skirt 8-inch v1.ipt]
2016-07-12 Nozzle BOM
    [Nozzle BOM.xlsx]
2016-07-13 Remaining 8 inch Nozzle CAD Files
    [Graphite 8-inch v1.0002.ipt, Graphite 8-inch v1.ipt, Nozzle 8-inch v1.0003.iam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]
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2016-07-19 Version 3 Nozzle CAD
    [Carrier.0001.ipt, Carrier.ipt, Graphite.0001.ipt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]
2016-07-20 Forward bulkhead
    [Forward Bulkhead.ipt]
2016-07-20 Edits for 7.5" fit of Retainer and Carrier
    [Carrier.0001.ipt, Carrier.0002.ipt, Carrier.ipt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]
2016-07-21 Increase OD of Nozzle parts
    [8 in AL casing.ipt, 8 in Casting Tube.ipt, 8 in Phenolic Linter.ipt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]
2016-07-26 Final Nozzle CAD and Renaming
    [Carrier Master Sketch.0001.ipt, Carrier Master Sketch.ipt, Carrier.0003.ipt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]
2016-08-21 Flight Sim
    added python project to simulate flight of rocket
    [Updated.NM-Q-8in-Motor-Prop-Calcs (1).xlsx]
2016-08-21 Release #1001-001
    8-inch motor calc release document
    [Q-8in-motor_calc.xlsx]
2016-08-26 cflannery sandbox
    [Q-8in-motor_calc.xlsx]
2016-08-30 organization and nozzle rev01
    [8 in AL casing.ipt, 8 in Casting Tube.ipt, 8 in Phenolic Linter.ipt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]
2016-09-03 organization and Nozzle Tag
    [Q-8in-motor_calc.xlsx]
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2016-10-09 Adding References; Nozzle Edits
    [8 in Phenolic Linter.0001.ipt, 8 in Phenolic Linter.ipt, Carrier Master Sketch.0002.ipt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]
2016-10-16 upload CAD files
    [Aerospike base.ipt, Spike tip.ipt, aerospike assembly.iam]
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2016-10-17 [Organization] Aerospike Project
    [Aerospike base.ipt, Spike tip.ipt, aerospike assembly.0001.iam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]
2016-10-18 fixing error with graphite sketch in master sketch.ipt
    [Master Sketch.0005.ipt, Master Sketch.0006.ipt, Master Sketch.ipt]
2016-10-18 updated sketch with 2part phenolic
    [Master Sketch.0006.ipt, Master Sketch.0007.ipt, Master Sketch.ipt]
2016-10-18 nozzle assembly
    [Aluminum_Carrier.0001.ipt, Aluminum_Carrier.ipt, AviBay.iam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]
2016-10-20 nozzle redesign
    [Aluminum_Carrier.ipt, Master Sketch.0008.ipt, Master Sketch.ipt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]
2016-10-20 [WIP] Drawing Template
    [Aluminum_Carrier.0001.dwg, Aluminum_Carrier.dwg]
2016-10-20 [Design] Drawing Template
    [Aluminum_Carrier.0001.dwg, Aluminum_Carrier.0003.dwg, Aluminum_Carrier.dwg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]
2016-10-21 [Design] Minor Edits to Graphite (GD&T) Drawing
    [Drawing Template (AutoCAD).0001.dwg, GRAPHITE.0011.idw, GRAPHITE.idw]
2016-10-22 [Design] Moving updated parts from Lifecycle
    [Aluminum_Carrier.0001.ipt, Aluminum_Carrier.0002.ipt, GRAPHITE.0011.idw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]
2016-10-23 adding ttemp work with full vehicle
    [Intrepid.0002.iam, Intrepid.iam, Master Sketch.ipt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]
2016-10-23 nozzle design space
    [aluminum.0004.ipt, aluminum.ipt, aluminum_retainer.0001.ipt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]
2016-10-24 [Design] WIP drawings
    [ALUMINUM CARRIER.0001.dwg, ALUMINUM CARRIER.dwg, ALUMINUM RETAINER.0005.dwg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]
2016-10-24 [Analysis] Temp Work
    [nozzle.iam]
2016-10-30 Intrepid CAD updates
    [8 in AL casing.ipt, 8 in Casting Tube.ipt, 8 in Phenolic Linter.0002.ipt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]
2016-11-01 nozzle updates
    [graphite.0001_1.ipt, graphite.ipt, graphite_OLD.ipt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]
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2016-11-02 moving refs back to original location and updating presentation
    [BatesCalc2K_template.xls, nozzle 8in version 1.ipt]
2016-11-04 [Design] WIP Section Adaptor
    [Section Adaptor Calculations.xlsx, Section Adaptor WIP.ipt]
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2016-11-08 Add files via upload
    Graphite material and properties added.
    [graphite.ipt]
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2016-11-08 cad and analysis updates
    [Q-8in-motor_calc.xlsx, motor.0004.iam, motor.0005.iam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]
2016-11-08 Initial Avionics Bay Designs
    The initial designs of the av bay, to be refined once I can open the intrepid.iam file and calculate the exact dimensions. It will also need to be refined once we know what is going into it and how i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
    [Avi Bay Lid.ipt, Avi Bay Start.iam, Avi Bay Steel.ipt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]
2016-11-13 Add files via upload
    These are the modified versions of the previous Inventor Files for the camera mount published on 11/13/16
    [bottom camera cover.ipt, camera holder design.iam, top camera cover.ipt]
